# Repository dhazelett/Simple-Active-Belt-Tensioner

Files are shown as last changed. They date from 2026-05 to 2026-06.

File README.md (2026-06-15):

> 📢 **Important:** This is a _pre-release_ of the project and considered to be under active development and testing. If you're not prepared to do some tinkering and/or deal with initial usability issues, it is recommended that you do not attempt to build it right now and instead wait for the `v1.0` release

SABT Logo

Diagram

# Simple Active Belt Tensioner

A haptic device for sim racing, designed specifically for people who do not have a background in software or electronics.

It requires **no soldering or programming** and can be built for **as little as ~215 GBP** _including the harness_.

## What Is It?

Introduction Video (https://youtu.be/b3R1tQvu-o4)

An _active belt tensioner_ is a device that attaches between your sim rig and the anchor points of your racing harness. It dynamically tensions the harness in response to game telemetry; giving a sense of the forces you'd be experencing in a vehicle when changing speed, braking, cornering and jumping/landing.

It works with **any game fully supported by [SimHub](https://www.simhubdash.com/)**, but the current software is designed primarily for racing games and simulators.

This project consists of three parts:
- A shopping list of [components](#what-does-it-cost), readily available from online sellers
- Printable [parts](/Printables/) and instructions on how to assemble them
- A _SimHub_ plugin that controls the hardware and allows customisation of the effects

The printable files and software are **completely free** (except the required [SimHub License](https://www.simhubdash.com/get-a-license/)). The printed part designs are `CERN-OHL-P` licensed (open-source), and the software is `MIT` licensed, which essentially means you can do what you like with either; including selling printed/machined parts kits.

### Design Goals
- Lowest Practical Cost
- Minimal Parts & Tools
- No Soldering
- No Programming
- No 'Reclaimed' Parts
- Direct-Drive (FOC/BLDC) Performance & Flexibility

## Who Is It For?

Anyone with a sim rig that desires a more immersive experience. It's a plug-and-play design that requires no soldering or programming, so virtually anyone can build it.

Note that you'll need either an _aluminium profile_ (e.g. [GT Omega Prime](https://www.gtomega.co.uk/products/prime-cockpit)) or _2" tubular steel_ (e.g. [GT Omega Titan](https://www.gtomega.co.uk/products/titan-cockpit)) sim rig frame to mount this using the available brackets. Mounting to other types of rig is possible, but you'll need to design and fabricate your own brackets (or [get in touch](mailto:sabt@georgewilkins.co.uk) with me). _Folding-seat_ rigs (e.g. [Playseat Challenge](https://www.playseat.com/)) are _not suitable_.

I would recommend installing tactile transducers (bass shakers) before embarking on belt tensioners and other more exotic haptic systems. Transducers are by far the simplest and cheapest way of adding real immersion to your experience. They provide detail that belt tensioners cannot (road bumps, curbs, etc), while tensioners provide constant forces that transducers cannot (braking, cornering, etc).

### Community Builds
Several members of the sim racing community have [provided photographs](https://photos.app.goo.gl/ju7rso1PFKGxnRhJ8) of their SABT builds. Many have also _forked_ the project and customised it to their needs.

If you build a SABT, you're encouraged to photograph and document your completed installation. A good way to do that is by [creating a new](https://github.com/GeorgeWilkins/Simple-Active-Belt-Tensioner/discussions/new?category=sabt-builds) GitHub discussion.

## What Does It Cost?

If you have your own 3D printer, as little as **215 GBP** including taxes and delivery. If not, **250~300 GBP** depending on your choice of printed parts supplier.

### Purchased Parts
| Price (GBP) | Part | Notes |
| - | - | - |
| 120 | 2 x Motors | Provides the tensioning force |
| 20 | Controller | Provides USB control of the motors |
| 6 | 2 x Bearings | Allows the pulley covers to rotate smoothly |
| 7 | Screw & Nut Set | Provides every needed fastener in one set (with _many_ spares) |
| 5 | 1M Cord | A low-friction cord that winds around the pulleys (attached at the other end to your belts) |
| 20 | Power Supply | Provides DC power to the motors |
| 12 | Back Driving Protection Unit | Prevents power-supply resets if the motors are back-driven (**optional but recommended**) |
| 25 | 5-Point 2" Harness | A low-cost Aliexpress model or used/expired FIA harness |
| **215** | **Total** | ...excluding printables |

There is a [detailed parts list](/INSTRUCTIONS.md#motors-electronics--fixings) with sources in the build guide.

### Printing Options
| Price (GBP) | Method | Notes |
| - | - | - |
| 5~10 | Self-Print | Roughly 200g or 75M of filament |
| 30~60 | FDM Service | Assuming an _eBay-tier_ printing provider, not a professional company |
| 60~90 | MJF/SLS Service | [JLC3DP](http://jlc3dp.com/) and [3DPrintUK](http://3dprint-uk.co.uk/) used for reference pricing (nylon dyed black with peening) |

### Other Costs
Note that you will also need [SimHub Licensed Edition](https://www.simhubdash.com/get-a-license/) (currently **8 EUR** or more) to use this device. If you're reading this, you almost certainly already have it.

## How Does It Work?

The two motors are anchored to your rig with printed brackets. A self-orienting pulley is attached to the face of each motor.

The ends of each shoulder belt are attached to lengths UHMWPE/Dyneema cord, which are wrapped around each motor pulley.

When SimHub sends game telemetry to our plugin, it converts this into torque commands and send them to the motors over a serial connection.

## How Does It Perform?

Since we're using high-quality BLDC/FOC integrated servo motors, the effects are applied directly as _force_ (torque) rather than emulated by moving the belts a fixed distance, as with some DIY tensioners based on RC servos.

The benefits of this are:
- Smooth and silent operation
- Compact & clean design
- Auto-adjusting of the harness (adjustable idle tension)

The maximum force appliable by these motors with the current pulley design is about **10Kgf per belt**, putting us right around the rated mechanical loading for each motor. Imagine having **~10Kg of weights** attached to each belt hanging down from the back of your seat, and you'll get the idea.

This is plenty to give extra immersion and feedback, but significantly less than you'd feel in a real vehicle at motorsport velocities.

For comparison, the [QS-BT1](https://qubicsystem.com/product/qs-bt1) claims _"20.5kg per channel"_, but is a considerably larger and costs six times more.

Note that this system conveys progressive constant forces (cornering, braking, etc) rather than fine details (road texture, track kerbs, etc). For the latter, you should install one or more tactile transducers. The two work together to imply the sensation of movement without a costly motion simulator.

[Force Testing.webm](https://github.com/user-attachments/assets/be7b9d7a-be3f-46f7-abf1-9659297854bb)

## Anything I Should Be Aware Of?

There is considerable variation in rig, seat and harness designs, so I cannot anticipate every possible configuration. You'll need to decide if this system is suitable for your rig by looking at the installations examples and instructions.

Of particular note:
- The belt clamp designs are intended for 2" wide belts of up to 2MM thickness. If your belts are wider or thicker than this, you will need to modify the design (or let me know and I'll create additional designs)
- The need for belt rollers depends on the seat design. In many cases applying low-friction tape is sufficient. A 'universal' [Belt Roller](INSTRUCTIONS.md#belt-rollers) design is included should you wish to use it
- The system includes a design for a [Back Driving Protection Unit](INSTRUCTIONS.md#back-driving-protection), which prevents your power supply's protection circuitry from tripping when the motors are back-driven (e.g. by pulling fast on the belts). This is an optional component, but highly recommended. A _zero-soldering solution_ is available, but even the soldered version is very simple to assemble
- Although the motors and driver board can tolerate up to `24V` supply, I've found that `15V` is a good compromise. Operating at the maximum `24V` is not reccommended, because any voltage spikes risk damaging the motors. Common `19V` laptop power supplies have been tested and work; but the higher the voltage, the greater the risk of damage

## Is It Safe?

This is an open-source project involving powerful motors, pinch points and moving belts attached to your body.

⚠️ **No claims are made regarding the safety of this device. You are responsible for ensuring its safe use and no liability is accepted by the creator(s) for any damage or injury caused by this device.**

With that said, design measures have been taken with safety in mind. See [SAFETY.md](SAFETY.md) for details.

## How Do I Get Started?

Read through the [instructions](/INSTRUCTIONS.md) to get a better idea of what's involved and how to proceed.

> 📢 **Important:** This is a _pre-release_ of the project and considered to be under active development and testing. If you're not prepared to do some tinkering and/or deal with initial usability issues, it is recommended that you do not attempt to build it right now and instead wait for the `v1.0` release

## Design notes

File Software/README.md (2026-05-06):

# Software

There are two things you'll need to use this belt tensioner:
- [SimHub](https://www.simhubdash.com/) and a [License](https://www.simhubdash.com/get-a-license/) for 60FPS telemetry data
- The project's SimHub plugin, which must be copied into SimHub's installation directory

## Downloading SimHub

SimHub is going to already be on your machine or at least familiar to you if you have a sim rig. In case it's not, it's a popular utility in the Sim Racing community that collates and normalises telemtery data from various games and simulators, making it available to many devices and plugins. Our tensioner uses that telemetry to determine how much tension to apply to the belt at any given moment.

1. Go to [https://www.simhubdash.com/](https://www.simhubdash.com/) and click on `Download now` or the `Download` link at the top of the page
2. You'll see a large button, labelled something like `Download SimHub vX.X.X`, which will start the download when clicked
3. Unzip the downloaded file and run the executable within to install SimHub on your computer
4. Run SimHub at least once before attempting to install the plugin

## Licensing Simhub

The free version of SimHub offers 10Hz telemetry updates, which is sufficient for some devicces; but not for our tensioner. We'll need to buy a license to unlock 60Hz updates. It's cheap (as little as 8 EUR for a perpetual license) and absolutely worth the money.

Note that you do not need a _'Motion License'_ to use this tensioner; that is a more costly thing for full motion rigs. The regular license is sufficient for our needs.

1. Go to [https://www.simhubdash.com/](https://www.simhubdash.com/) and click on the `Get a license` link at the top of the page
2. Enter your details and complete payment
3. Grab the key from the e-mail you're sent and enter it into `Settings` > `General` > `Licenses` within SimHub
4. Once done you should see `Status: Licensed` at the bottom of the SimHub window

## Downloading & Installing The Plugin

1. Make sure _SimHub_ is closed before proceeding
2. Download the [SABT SimHub Plugin.zip](SABT%20SimHub%20Plugin.zip) file
3. Unzip the downloaded file, which will contain a `.dll` file (the plugin itself) and a `/Languages/` folder
3. Copy both into your SimHub installation directory (e.g. `C:\Program Files\SimHub`)
4. Open _SimHub_, which should then recognise the plugin and load it
5. Click on the `Simple Active Belt Tensioner` plugin in the left-hand menu and configure it as you like

You can change the language of the plugin (and SimHub itself) from `Settings` > `General` > `Language`.

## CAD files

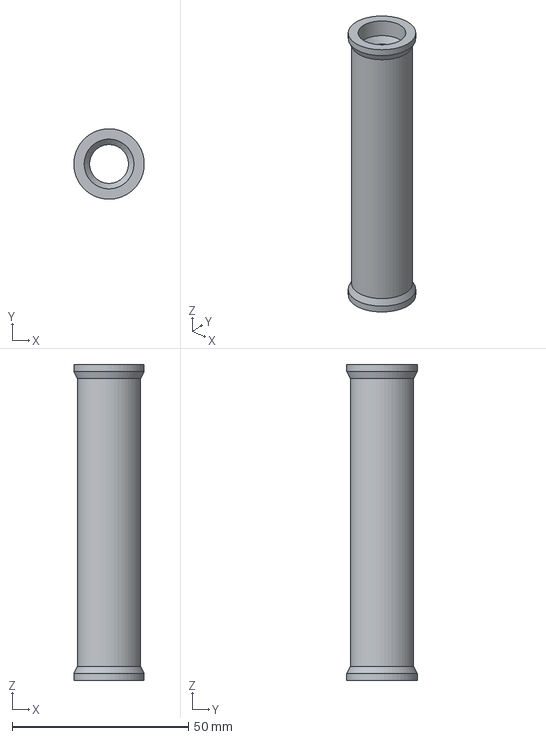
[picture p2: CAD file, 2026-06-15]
Printables/Belt Roller/Belt Roller (Roller).step
20.0 x 20.0 x 89.6 mm

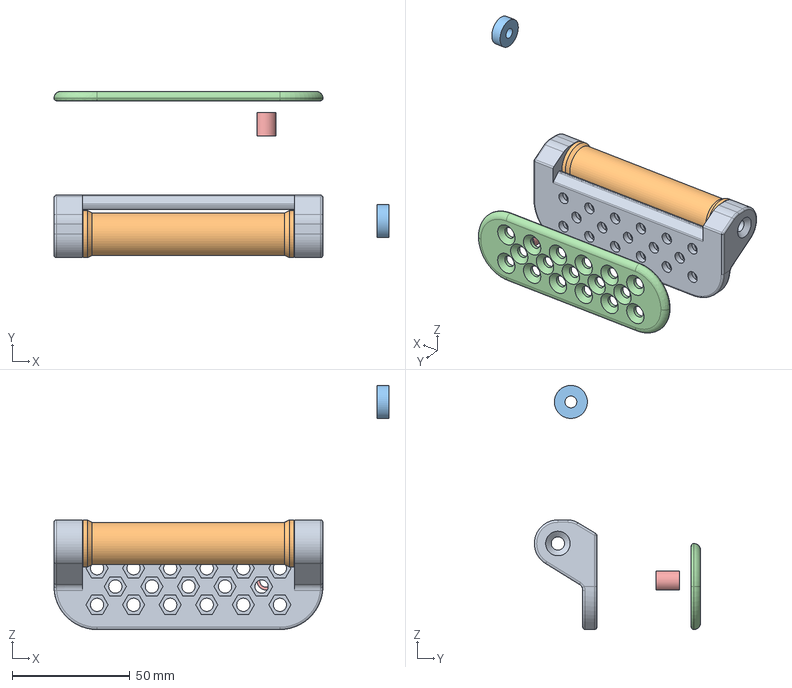
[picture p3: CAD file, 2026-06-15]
Sources/Printables/Belt Roller.FCStd
142.0 x 70.5 x 103.5 mm
Bracket
Roller
Bearing 5x14x5
Plate
Spacer

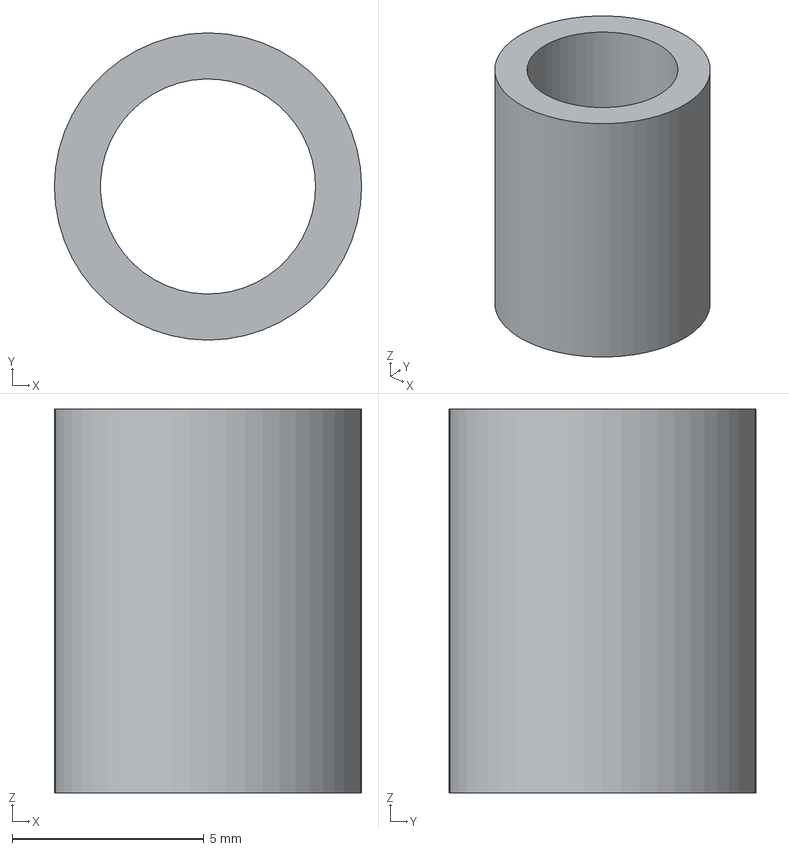
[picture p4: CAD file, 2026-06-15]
Printables/Belt Roller/Belt Roller (Spacer).step
8.00 x 8.00 x 10.0 mm

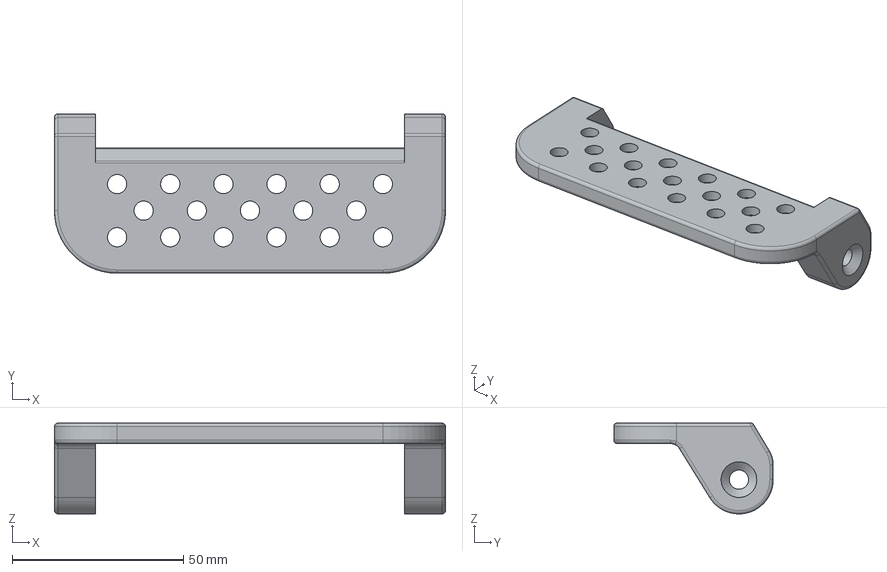
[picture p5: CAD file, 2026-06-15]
Printables/Belt Roller/Belt Roller (Bracket).step
114.0 x 46.5 x 26.5 mm

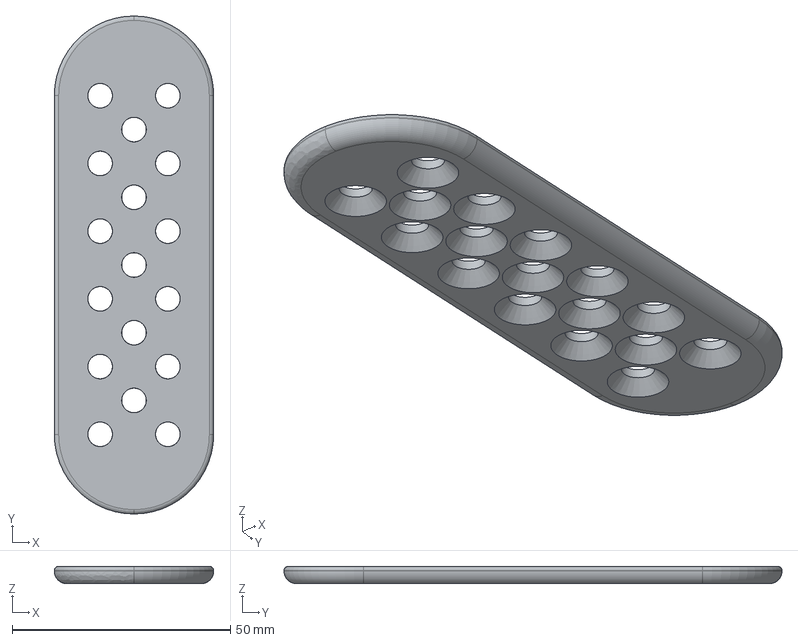
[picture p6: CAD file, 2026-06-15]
Printables/Belt Roller/Belt Roller (Plate).step
36.5 x 114.0 x 4.00 mm

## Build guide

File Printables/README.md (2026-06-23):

# Printables

The files in this directory and its sub-directories are what you need to print (or to have printed by a third party) to complete the kit.

Since there are a couple of options to choose from, you should read this before selecting and printing (or ordering) your parts.

### Choosing Your Brackets

Flat Motor Bracket (30~40mm Hole Spacing)

There are two main types of sim rig frame; _tubular_ and _profile_ (also known as _aluminium extrustion_):
- **Profile rigs** (e.g. [GT Omega Prime](https://www.gtomega.co.uk/products/prime-cockpit)) typically use `40-Series` aluminium extrusion that is bolted together in a modular fashion
- **Tubular frames** (e.g. [GT Omega Titan](https://www.gtomega.co.uk/products/titan-cockpit)) typically use `2"` steel tubing that is mandrel-bent into shape and welded together

If you have a _profile rig_, choose from the `Corner` or `Flat` profile bracket designs. In the latter case:
- The smaller `30~40mm Hole Spacing` version is suitable for most standard `30-series` and `40-series` profile
- The larger `50~90mm Hole Spacing` version is intended for larger or more unusual profiles

There are optional `Extra Tall` variants that provide an additional `50mm` distance between the motor and the mounting surface, for situations where you need to clear obstructions. These obviously use more material and will flex more under load. Use the standard height versions if you can.

If you have a _tubular frame_, choose the `Tube` clamp bracket design (which integrates with a commercial [truss clamp](https://www.amazon.co.uk/dp/B07DP1FK33) to attach to the tube).

You only need to print _two_ of a single type of bracket. The designs are all symetrical.

### Choosing Your Belt Clamps

Since there are a variety of belt types and terminations, a few options are available:
- **End Clamp**: This is designed to clamp the plain end of an unterminated 2" belt (suitable for bare belt ends, or belts you are happy to shorten to the ideal length)
- **Loop Clamp**: This is designed to loop through a 2" belt (up to 4mm thick) and secure back on itself using a standard belt buckle (likely to have come with your hanress)
- **Through Clamp**: This is designed to clamp anywhere along a 2" belt without needing to shorten or terminate the belt itself

The **Through Clamp** is probably the easiest to integrate, while the **End Clamp** is the neatest; but needing the belts to be shortened specifically for the tensioner (or shortened non-destructively with buckles).

### Opting For Belt Rollers

There's a lot of variation in seat design. In cases where the belt guides have horizontal bottom surfaces (perpendicular to your pulley cords), you don't _need_ belt rollers; the belts will just slide through the guides without issue. In this case low-friction tape _is_ recommended for a smoother experience and to protect your belt guides.

However with irregular or angled belt guides, you may run into issues with the belts bunching up in the corners of the guides and not sliding smoothly. For such cases, you can print and assemble two 'universal' [belt rollers](/Printables/Belt%20Roller/), which have been designed with an array of mounting holes to accommodate most belt guide shapes and angles.

These will not work well with curved belt guides (where they match the curvature of the seat). In such cases you may need to design your own version of the roller. You can use the [FreeCAD source file](/Sources/Printables/Belt%20Roller.FCStd) as a reference and starting point if so.

## Printables List

Regardless of your choices above, you should end up with:
- 2x Belt `End`|`Loop`|`Through` Clamp (Front)
- 2x Belt `End`|`Loop`|`Through` Clamp (Rear)
- 1x Controller Case (Top)
- 1x Controller Case (Base)
- 2x `Corner`|`Flat`|`Tube` Motor Bracket
- 2x Bearing Pulley (Cover)
- 2x Bearing Pulley (Face)
- 2x Bearing Pulley (Hub)

If you're making the [Back-Driving Protection Unit](/INSTRUCTIONS.md#back-driving-protection) you'll additionally need:
- 1x Back-Driving Protection Case (Top)
- 1x Back-Driving Protection Case (Base)

If you're making the [Belt Rollers](/Belt%20Rollers) you'll additionally need:
- 2x Belt Roller (Bracket)
- 2x Belt Roller (Plate)
- 2x Belt Roller (Roller)
- 4~8x Belt Roller (Spacer) \*

\* These are intended to be vertically scaled in your slicer software to be slightly shorter (by `~0.5mm`) than the depth of your belt guide (usually `12~40mm`). They help to prevent the bracket and plate from bending once clamped and also protect your belt guide plastics from the screw threads. It is recommended that you print the rollers and spacers together (in a vertical orientation) and the bracket and plate together (in a horizontal orientation).

### Self Printing

Obviously if you have your own 3D printer, you can print these yourself. These parts have been designed with hobby FDM printers in mind (not SLA/DLP/MSLA/LCD resin printers).

I've used [DEEPLE PLA Plus](https://www.amazon.co.uk/dp/B0F66H47J8) on my Bambu H2S for all of my own parts; but virtually _any_ strong PLA/ABS/PETG filament should be fine. Fibre-reinforced filament is okay for the mounting brackets but _not reccommended_ for the pulley parts.

As for printing settings, I would suggest:
| Setting | Value |
| - | - |
| Layer Height | `0.16` |
| Walls | `7` |
| Top Shell Layers | `7` |
| Bottom Shell Layers | `7` |
| Infill Density | `30%` |
| Supports | `Manual` |

Manually add supports to the counterbored bolt & nut holes _only_. They aren't needed anywhere else.

The above takes about **8 hours** on my H2S if printing everything at once. It uses about 75M of filament, or ~230g of PLA. I'd suggest you do the parts in smaller batchces though, to minimise wastage if something goes wrong during the print.

### Third-Party Printing

There are plenty of hobbyists on eBay offering low-cost FDM printing. Quality will depend very much on the individual seller.

If you want a more commercial-looking end result, there are companies running SLS/MJF machines which produce Nylon parts for reasonable money:
- [3DPrintUK](https://3dprint-uk.co.uk) are a provider of SLS/MJF Nylon parts in the UK. They have an instant quotation system that will give you a price right away (~**90 GBP** at the time of writing)
- [JLC3DP](https://jlc3dp.com) offer a similar service out of China with delivery to most countries

I've had test prints done in MJF Nylon PA12 (dyed black & shot peened) which came out great, but as with FDM printing, getting the tolerances correct for the press-fit bearings requires some trial and error.

FDM PLA (Left) &amp; MJF Nylon (Right)
FDM PLA (Left) &amp; MJF Nylon (Right)

### CNC Machining

At some point I'd love to see machined aluminium parts become available; but the parts included in this repository are very much designed for FDM printing, not CNC subtractive manufacturing.

Some of the parts would need to be adapted considerably to work with the latter process.

If you have the means to do this and want to make them available, please get in touch.

## Downloading

The printable files are provided in the `STEP` format. This provides the highest quality of geometry while being compatible with all major 3D printer slicing sofware _and_ commercial printing and CNC services.

GitHub treats these as _text_ files, so displays their contents rather than offering a download. To download a printable `STEP` file, use the `Download Raw File` option, which looks like a _tray and arrow_ icon:
Download STEP File

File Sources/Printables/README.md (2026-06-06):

# FreeCAD Source Files

If you're here looking for things to print, _you're in the wrong place_; go [here](/Printables) instead.

These files are the original [FreeCAD](https://www.freecad.org/) design files from which the printable `.STEP` files are generated. You'll only need these if you intend to change the designs of the parts.

| File | Part | Description |
| - | - | - |
| [Controller Case.FCStd](Controller%20Case.FCStd) | Electronics Case | The two halves of the **controller case** |
| [Back-Driving Protection Case.FCStd](Back-Driving%20Protection%20Case.FCStd) | Electronics Case | The two halves of the **back-driving protection unit case** |
| [Belt Roller.FCStd](Belt%20Roller.FCStd) | Belt Roller | The **belt roller** assembly |
| [Belt End Clamp.FCStd](Belt%20End%20Clamp.FCStd) | Belt Clamp | The two halves of a **belt clamp** (suitable for clamping the plain end of a 2" belt) |
| [Belt Loop Clamp.FCStd](Belt%20Loop%20Clamp.FCStd) | Belt Clamp | The two halves of a **belt clamp** (suitable for looping through a 2" belt) |
| [Belt Through Clamp.FCStd](Belt%20Through%20Clamp.FCStd) | Belt Clamp | The two halves of a **belt clamp** (suitable for clamping anywhere along a 2" belt) |
| [Corner Motor Bracket.FCStd](Corner%20Motor%20Bracket.FCStd) | Motor Bracket | A motor bracket designed to be **corner-mounted** to `30MM` or `40MM` aluminium profile |
| [Corner Motor Bracket (Extra Tall).FCStd](Corner%20Motor%20Bracket%20(Extra%20Tall).FCStd) | Motor Bracket | A motor bracket designed to be **corner-mounted** to `30MM` or `40MM` aluminium profile, with an additional `50mm` of motor distance from the mounting surface |
| [Flat Motor Bracket (30~40mm Hole Spacing).FCStd](Flat%20Motor%20Bracket%20(30~40mm%20Hole%20Spacing).FCStd) | Motor Bracket | A motor bracket designed to be **flat-mounted** to `30MM` or `40MM` aluminium profile |
| [Flat Motor Bracket (30~40mm Hole Spacing, Extra Tall).FCStd](Flat%20Motor%20Bracket%20(30~40mm%20Hole%20Spacing,%20Extra%20Tall).FCStd) | Motor Bracket | A motor bracket designed to be **flat-mounted** to `30MM` or `40MM` aluminium profile, with an additional `50mm` of motor distance from the mounting surface |
| [Flat Motor Bracket (50~90mm Hole Spacing).FCStd](Flat%20Motor%20Bracket%20(50~90mm%20Hole%20Spacing).FCStd) | Motor Bracket | A motor bracket designed to be **flat-mounted** to larger or more unusual aluminium profiles |
| [Flat Motor Bracket (50~90mm Hole Spacing, Extra Tall).FCStd](Flat%20Motor%20Bracket%20(50~90mm%20Hole%20Spacing,%20Extra%20Tall).FCStd) | Motor Bracket | A motor bracket designed to be **flat-mounted** to larger or more unusual aluminium profiles, with an additional `50mm` of motor distance from the mounting surface |
| [Tube Motor Bracket.FCStd](Tube%20Motor%20Bracket.FCStd) | Motor Bracket | A motor bracket designed to be **clamp-mounted** to `50MM` tube (requires [truss clamp](https://www.amazon.co.uk/dp/B07DP1FK33)) |
| [Pulley.FCStd](Pulley.FCStd) | Pulley Assembly | The **pulley** cover, hub and face parts |

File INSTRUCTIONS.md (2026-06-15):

# Instructions

Everything you need to know about building a tensioner of your own is in this document. Please make sure you at least skim through each section before proceeding.

## Printed Parts

See the [/Printables/](/Printables/) directory to obtain the printable files, and detailed information on printing them. Make sure you read through this document and note which printable parts you _actually need_.

## Ordering Components
### Motors, Electronics & Fixings

You should be able to order the _Waveshare_ [motors](https://www.waveshare.com/wiki/DDSM115) and [control board](http://www.waveshare.com/wiki/DDSM_Driver_HAT_(A)) from the same supplier, as they are almost always stocked together. They are designed for robotics projects, so those kinds of retailers are your best bet.

The rest of the parts can be obtained from virtually anywhere, including [Amazon](https://www.amazon.co.uk) or [AliExpress](https://www.aliexpress.com). Where I've linked to particular products, these are not endorsements or items I've tested; simply representative examples. Shop around, as prices change constantly...

| Guide Price | Part | Description | Example |
| - | - | - | - |
| `60 GBP` `x2` | 2 x `DDSM115` Motors | Waveshare BLDC FOC servo motors | [PiHut UK](https://thepihut.com/products/ddsm115-direct-drive-servo-motor) |
| `20 GBP` | `DDSM Driver HAT (A)` | Waveshare Controller Board (Version 'A' For `DDSM115` and `DDSM210`) | [PiHut UK](https://thepihut.com/products/ddsm-hub-motor-driver-board) |
| `6 GBP` | 2 x `6706` Bearings | `30x37x4mm` bearings for the pulleys | [Amazon UK](https://www.amazon.co.uk/dp/B0D4DN3RW8) |
| `7 GBP` | `M2.5` Screw & Nut Set | Eight `M2.5x16` (or `M2.5x18`) + eight `M2.5x10` + six `M2.5x12` + six `M2.5x20` + sixteen `M2.5` nuts | [Amazon UK](https://www.amazon.co.uk/dp/B0FSWHZPGD) |
| `5 GBP` | `~1M` UHMWPE/Dyneema Cord | The low-friction high-strength cord for the pulleys (`1.6~2.0MM` Diameter) | (any by-the-metre seller; eBay, etc) |
| `20 GBP` | `15V` `90W` DC Power Supply | The power supply for the board and motors (standard `5.5x2.5MM` centre-positive barrel plug) | [Amazon UK](https://www.amazon.co.uk/dp/B09RHC7QG9) |
| `25 GBP` | 5-Point `2"` Harness | A low-cost Aliexpress model or used/expired FIA harness | [AliExpress](https://www.aliexpress.com/item/1005008051519590.html) |

> 📢 **Important:**
> - The `DDSM115` motors are _sometimes_ sold in **pairs**. Make sure you're only buying _two motors_, not _two sets of two_
> - There are multiple motor models in the `DDSMXXX` series. Make sure you're buying the [DDSM115](https://www.waveshare.com/wiki/DDSM115)
> - There are multiple control board models of similar appearance. Make sure you're buying the [DDSM Driver HAT (A)](https://www.waveshare.com/wiki/DDSM_Driver_HAT_(A))
> - If using the _tubular_ brackets, you'll need to order two [2" Truss Clamps](https://www.amazon.co.uk/dp/B07DP1FK33), a pair of [`M10` Nuts](https://www.amazon.co.uk/dp/B0CGQVMP45) and [`M10x16MM` Low-Profile Bolts](https://www.amazon.co.uk/dp/B0DYHY2DHB)

### Belt Rollers

These are considered to be _optional_, but are usually required for seats with angled or irregularly shaped belt guides. They cost little to build, so are _recommended_ if you have any doubts about your seat's belt guide design or want maximum performance.

| Guide Price | Part | Description | Example |
| - | - | - | - |
| `5 GBP` | 4 x `605` Bearings | `5x14x5mm` bearings for the rollers | [Amazon UK](https://www.amazon.co.uk/dp/B0CZ8DJ6YM) / [Amazon UK](https://www.amazon.co.uk/dp/B0F6LNSC75) |
| `5 GBP` | 8 x `M5` Fully-Threaded Countersunk Bolts | Length depends on seat belt guide depth | [Amazon UK](https://www.amazon.co.uk/dp/B0C97LXKBP) |
| `5 GBP` | 8 x `M5` Hex Nuts (`8mm` WAF) | Must be `<5mm` thick | [Amazon UK](https://www.amazon.co.uk/dp/B0FMRFPWJ3) |

> 📢 **Important:**
> - Countersunk bolts are typically measured by their _entire length_ including the head
> - Measure your seat's belt guide/hole depth and _add_ `10mm`, rounding up to the nearest standard bolt length (e.g. my `39mm` belt guides need `50mm` bolts)
> - The bolts _must_ be fully threaded; otherwise you won't be able to use them for the roller axles
> - If you use bolts that are longer than needed, they may interfere with the belts and rollers

If _not_ using rollers, you can reduce friction (and wear) on your seat's belt loops if you apply some low-friction tape over the contact points. I've had success with [2-3/8" PTFE Tape](https://www.amazon.co.uk/dp/B0F3XKJW2V).

### Back-Driving Protection

You are _strongly encouraged_ to assemble and use this, as without it any rapid pulling on the belts may trigger the OVP/OCP within your power supply (as the motors act as _generators_ in this scenario) and disable tensioner functionality until time passes or a manual power supply reset is performed. There are a number of assembly and parts options detailed below. The [printable case](Printables/Back-Driving%20Protection%20Case) is designed to accommodate all of these options.

> ⚡ **Warning:** All of these options add a modest capacitance between the power supply and controller board. If you disconnect the protection unit, the capacitor may remain charged at up to `~15V` for a period of time. Do not touch or short the terminals at either end of the unit, as doing so **may cause a shock or damage equipment**.

The parts required will depend on your chosen option, but none should exceed `15 GBP` in cost:
- [Solderless + Ideal Diode](#solderless--ideal-diode): Using an ideal diode module with pre-soldered terminals
- [Soldered + Ideal Diode](#soldered--ideal-diode): Using an ideal diode module without terminals (requires soldering)
- [Discrete Schottky Diode](#discrete-schottky-diode): Using a discrete Schottky diode (requires _trickier_ soldering)

Back Driving Protection Options

#### Solderless + Ideal Diode

If you're at all uncomfortable with the idea of soldering or don't have the equipment, you can choose this option. You will need to cut and strip some wires, but no soldering is required.

We leverage the availability of premade 'Ideal Diode' modules with easy-to-use screw terminals and cheat a little by adding our capacitor across the output terminal, avoiding the need for any soldering at all.

| Guide Price | Part | Description | Example |
| - | - | - | - |
| `5 GBP` | Ideal Diode Module | A pre-made diode board with soldered screw terminals | [AliExpress](https://www.aliexpress.com/item/1005009419896467.html) |
| `5 GBP` | Capacitor | A `2200uF` `35V` electrolytic capacitor (just one; you'll have spares) | [Amazon UK](https://www.amazon.co.uk/dp/B07K87YFP9) |
| `5 GBP` | DC Cable | A `5.5x2.5mm` DC barrel plug to `XT60` adapter cable (or barrel-to-barrel extension)  | [Amazon UK](https://www.amazon.co.uk/dp/B0BPKNG672) or [Amazon UK](https://www.amazon.co.uk/dp/B0FJ8BKQCF) |

> 📢 **Important:** The printable case for the protection unit is intended for cables with a `5~5.5mm` external diameter, which is fairly typical. Any larger and you'll struggle to fit the cable into the ends of the case. Note also that the screw terminals on the diode board have a maximum gauge of roughly `10 AWG` (or `2.6mm` core diameter); though yours may vary.

The assembly instructions for this solderless option are included below under the [Assembly](#assembly) section.

#### Soldered + Ideal Diode

Soldered Option

This is essentially the same as the [Solderless + Ideal Diode](#solderless--ideal-diode) option; just using a premade 'Ideal Diode' module _without_ presoldered screw terimnals and soldering our wires and capacitor directly to the pads on the board.

As soldering jobs go this is very easy, and opens up many more options when it comes to 'Ideal Diode' modules. The one suggested for the solderless option can also be ordered without terminals and is a known good option; but you are not restricted to that specific module.

The main things you need to ensure of your chosen 'Ideal Diode' module are:
- The module actually blocks reverse current; not all such modules do (for 'OR-ing' purposes)
- The current handling exceeds `6A`
- The voltage handling exceeds `24V` (ideally `30V+`)
- The board has both `V+` and `GND` solder pads to make assembly easier (some omit the `GND` pads)

As long as these requirements are met, the module _should_ do the trick. These are some (unverified) examples:
- [Pololu 5382](https://www.pololu.com/product/5382)
- [Pololu 5383](https://www.pololu.com/product/5383)
- [Pololu 5388](https://www.pololu.com/product/5388)
- [Pololu 5389](https://www.pololu.com/product/5389)
- [Generic LM74700 Module](https://www.amazon.co.uk/dp/B0FNY9MWLX)
- [Generic 'Solar Diode' Module](https://www.amazon.co.uk/dp/B07QGW5J1H)

#### Discrete Schottky Diode

If you're a maker and familiar with electronics, a very simple circuit can be made using the same capacitor and any Schottky-like (e.g. SBR, SiC) diode with sufficient ratings. See above for the suggested values.

Strictly speaking this would be a downgrade from the 'Ideal Diode' style boards, but will still do the job just fine. Voltage drop is unlikely to be problematic with that class of diode, and the motors are wide-input.

See the diagrams above for a reference circuit design.

## Assembly

Depending on your choices above, some of these assembly instructions may not be relevant to you. Please read through the instructions and only follow the steps that are applicable to your build.

The photographs provided are for illustrative purposes and may not show the absolute latest part designs; don't worry if they aren't _exactly_ the same as the parts you've printed.

### Motors

| Step | Instructions | Illustration |
| :-: | :- | :-: |
| 1 | Since the motors are technically _wheels_, they come pre-fitted with rubber treads, which we need to remove.<br /><br />Unscrew the three `M2.5` bolts holding on motor face plate and remove it. You may need to remove a 'QA' sticker covering one of the screws.<br /><br />With the face plate removed, push the motor face (with the triangular hub) firmly with your thumbs, while holding the opposing face/rim of the tire with your fingers. Gradually working your way around the rim, moving small amounts at a time works best. | Wheel Motor |
| 2 | You'll be left with the bare motor. Keep the rubber tire, face plate and bolts safe though; in case you need to return the motors or repurpose them later. | Motor Without Tire |

### Pulleys

| Step | Instructions | Illustration |
| :-: | :- | :-: |
| 1 | Gather the four pulley parts; the bearing, the outer cover, the face plate and hub. | Pulley Parts |
| 2 | Press the bearing into the outer cover. This should be possible by hand. The accuracy/roughness of your print will dictate how easy this is.<br /><br />If the fit is too tight, use a hammer to _gently_ tap it in (alternating sides with each tap) or consider shaving away some material with a knife or file.<br /><br />If the fit is too loose, cut up a drinks can and shim around the edges of the bearing to fill in the gap (ensuring the shims do not protrude). | Inserting The BearingInserted Bearing |
| 3 | Insert the pulley face from the front so it sits inside the inner ring of the bearing. The notes above regarding fitting tolerances apply here too. | Face Inserted |
| 4 | Insert the pulley hub over the top, so that the triangular shape on the face part pushes into the triangular hole of the hub. They may pop together or be loose depending on the tolerances of your print (either is fine). The slot in the hub for the cord should be facing outward. | Hub Fitted |
| 6 | Cut a `0.5M` length of the _UHMWPE/Dyneema cord_ and tie a tight knot in the end, then remove any excess cord after the knot. | Knotting The Cord |
| 5 | Thread one end of the cord through one of the pulley cover holes. When assembling the _Left_ pulley, use the hole marked with `L` inside the pulley cover (or `R` for the _Right_ pulley). Push the knot into the cut-out in the pulley hub. It should stay in place relatively well. | Cord Inserted |
| 8 | Install the pulley onto the motor hub and insert and tighten three `M2.5x12MM` screws into the face plate. Make sure that the cord stays in the cut-out when doing so. | Installing The Pulley |

### Belt Clamps

| Step | Instructions | Illustration |
| :-: | --- | :-: |
| 1 | Gather the belt clamp parts; the four `M2.5x10` bolts, four `M2.5` nuts, and the front and rear plates. | Belt Clamp Parts |
| 1 | Insert `M2.5` nuts into the hexagonal holes on the underside of the rear clamp plate (as deeply as they will go). | Nuits Fitted |
| 2 | Tie a tight knot in other end of the cord you previously attached to the _Pulley_. Push the knot into the cut-out in the rear clamp plate, so the cord comes out the bottom. | Cord Fitted |
| 3 | Place the end of the harness belt into the rectangular detent of the rear clamp plate (it may overlap the knot; that's fine). Push the front clamp plate firmly down over both. | Belt PositionedClamp Applied |
| 4 | Keep pressure on the assembly while securing with the four `M2.5x10` bolts. Tighen each bolt partially in a circular pattern until they are all tight, rather than trying to fully tighten one at a time. | Tightening The Clamp |
| 5 | Once fully tightened, the two clamp parts should be fully touching with no visible gap between them. | Clamp TightenedClamp Fully Assembled |

### Brackets

| Step | Instructions | Illustration |
| :-: | --- | :-: |
| 1 | Gather the bracket parts; three `M2.5x20` bolts, the bracket and the motor (with or without pulley fitted). Since there are a number of bracket designs, the hardware needed to actually attach them to your rig will vary (but should be obvious if you already have a rig). | Bracket Parts |
| 1 | _Carefully_ feed the motor connectors and wires through the hole in the bracket. Bend back the smaller connector so you're not trying to push both through at once. | Folding Back The ConnectorWires Fed Through |
| 3 | Insert the motor stem into the socket on the braket. The shaft and socket are three-sided and symmetrical, so rotate it until it aligns with the socket and push in. As long as it sits fully into the socket, the angle doesn't matter. | Inserted The Motor |
| 2 | Secure the motor with the three `M2.5x20MM` bolts | Motor Bolted In |
| 3 | Attach the bracket to your rig frame. If using the _aluminium profile_ bracket designs, secure the bracket to your rig frame with suitable t-nuts and bolts. If using the tubular mount (with truss clamp), insert the `M10` nut into the printed backet slot, then secure it to the truss clamp with the `M10x16` bolt. | Assembled Bracket |

### Controller Board

| Step | Instructions | Illustration |
| :-: | --- | :-: |
| 1 | Gather the control board parts; the four `M2.5x16` bolts, four `M2.5` nuts, and the upper and lower shells. | Controller Board Parts |
| 2 | Flip the switch on the control board to the `USB` setting. | Switch Set To 'USB' |
| 3 | Insert `M2.5` nuts into the hexangonal holes on the underside of the lower printed case (as deeply as they will go). | Nuts Inserted |
| 4 | Insert the board into the lower half of the printed case. The _Raspberry Pi_ header on the rear may be a tight fit here; push down on the white circles either side of the header to press this in. | Board Inserted |
| 5 | Place the upper half of the case on top and secure with four `M2.5x16` bolts. | Case Assembled |

### Belt Rollers

| Step | Instructions | Illustration |
| :-: | --- | :-: |
| 1 | Gather the parts for each belt roller; the five `M5` bolts (length according to your belt guide depth), five `M5` nuts, three spacers, two `605` bearings, bracket, plate and roller. | Belt Roller Parts |
| 2 | Press-fit the bearings into the ends of the roller. | Fitting The Bearings |
| 3 | Insert two `M5` nuts into the inside faces of the bracket ends and thread in the `M5` bolts from the outside; no more than a couple turns (so their ends are flush with the nuts). | Inserting Nuts & Bolts |
| 4 | Position the roller between the bracket ends and start screwing in the bolts all the way, securing the roller in place. | Attaching The Roller |
| 5 | Take the partially assembled roller and remaining parts to your sim rig. | Partially Assembled |
| 6 | Establish where you'd like to mount the roller and which positioning holes you'll use. The roller must be as close to horizontal as possible and nideally cover the entire width of the belt guide hole. Horizontal guides only require two holes/bolts, while angled guides typically require three to prevent sideways movement. | Positioning |
| 7 | On the face plate, find the corresponding holes to the ones you previously chose and insert the `M5` bolts. Place the printed spacers over those. | Bolts & Spacers |
| 8 | Position the face plate inside the belt guide, with the bolts resting on the bottom face of the belt guide hole. At this point you may need to feed through your belt, as there may not be space to do so once the roller is fitted. | Face Plate |
| 9 | Line up the bracket with the face plate and bolts, then insert the `M5` nuts and tighten from the other side. The face plate and bracket should _lightly_ clamp to the front and back faces of the seat's belt guide. | Bracket Installation |
| 10 | Repeat for the other side and if you haven't already, feed the belts through and check that everything is moving freely. | Installed |

The choice of which holes to use is up to you and very much specific to your seat design. Below are some placement examples for common seat belt guide shapes. Note that horizontal belt guides can be fitted with only two `M5` positioning bolts, while angled guides usually need three to prevent sideways movement:

Belt Guide Shapes

### Back-Driving Protection

| Step | Instructions | Illustration |
| :-: | :- | :-: |
| 1 | Assemble the protection unit parts; the four `M2.5x16` bolts, four `M2.5` nuts, the capacitor, the diode board, the adapter cable and printed case. Cut the adapter cable in half as shown. | The Protection Unit Parts |
| 2 | Bend the capacitor legs as pictured, taking care not to damage the capacitor and noting the oritentation shown. If the legs of the screw terminals protrude significantly from the bottom of the board, take this opportunity to trim them down with some snips. | Preparing The Capacitor |
| 3 | Fully loosen the screw terminals. Insert the capacitor legs into the **output** screw terminals as shown (`GND` and `VOUT` on the board). with the capacitor `-` leg going into the board's `GND` as pictured. Do not tighten the terminals yet. | Fitting The Capacitor |
| 4 | Trim off roughly `6mm` of sheathing from the adapter cable ends and twist as shown. |  |
| 6 | Insert the bare wires into the screw terminals. The `XT60` cable should be on the **output** side and the round DC barrel cable should be on the **input** side. **Black** to `GND` and **red** to `VOUT` and `VIN`. Tighten up the screws as much as they will go. |  Inserting The Wires |
| 5 | Check for any stray or loose wires and adjust if needed. Install the unit into the printed case, taking care not to disturb the fitted wires. Make sure that the black outer sheath of the cable goes _completely inside_ the case as shown, so that the case lid can clamp down on it once closed. | Fitting Into The Case |
| 8 | Install the `M2.5x16MM` screws and nuts into the case and tighten as much as they will reasonably go. Ideally if you happen to have a multimeter, before attempting to power the controller board, check that the `XT60` connector produces the expected `15V` in the correct polarity (the **flat** side should be `+` and the **beveled** side `-`) when the power supply is connected to the dc barrel plug. |  The Completed Protection Unit |

## Wiring Up

Since the Waveshare board and motors are plug-and play, this is pretty straight forward.

If you're using the [Back-Driving Protection](#back-driving-protection), plug that into the control board (either the XT60 or DC Barrel sockets) and then into the power supply; otherwise just plug the power supply into the board directly.

If this is your first-time setup, your motors will need to be configured, so start with only a single motor plugged into the board. The plugin will tell you when to plug in the second motor.

It doesn't matter which of the exposed connectors on the top of the board you use for each motor. Make sure you've fully seated both the two-pin power plug and four-pin data plug.

Plug your USB type-c cable (one is supplied with the board) into the USB socket closest to the power connectors (marked `DDSM` on the board). If you use the other USB socket, it won't work.

If everything is connected correctly, the board will be detected by the SimHub plugin. No drivers are required.

> ⚠️ **Important:** Do not attempt to power or test the motors while not securely installed on the rig. If they start rotating while loose, they'll move around and potentially destroy themselves, the control board and the surface they are on

## Adjustment

Pulley & USB Port Guidance (https://www.youtube.com/watch?v=9At6qqblOZY)

If you already have a harness, you'll be accustomed to tightening it up with the buckles/straps it has. **You don't need to do that with this tensioner**, since it pre-tensions the harness for you (see `Idle Tension` in the `Tension` tab of the plugin).

However when first setting up the tensioner, you'll need to ensure the following:
- There is enough _plain belt_ (with no buckles or wider sections) to slide through the belt holes on your seat unhindered (allow for at least `20CM` of movement)
- Any excess belt is tucked/buckled away such that it does not catch or rub on anything

If you have excess shoulder belt length, you should run it through the seat holes and then buckle it back upon itself behind the seat (just above where you apply the tensioner's cord clamps).

Belt Clamps

The method of adjustment may depend on your chosen belt clamp design:
- **End Clamps**: These require the shortening of the harness shoulder belts, which is _strongly discouraged_ until you're 100% happy with your setup. Try using the belt buckles that likely came with your harness to make non-destructive adjustments to length first
- **Through Clamps**: Loosen the clamp bolts and simply slide the clamp up or down the length of the harness shoulder belts, then retighten in the desired location
- **Loop Clamps**: You'll already be using belt buckles to secure the looped harness shoulder belts against themselves, so simply adjust those buckles until you achieve the desired lengths

Adjustment

For reference, a _single turn_ of the pulley is about `~10CM` of cord. This is useful when working out how much cord you have wrapped around the enclosed pulley.

Since our harness is going to be self-adjusting (at least in the shoulders), we should make sure we have `~25CM` of cord between the belt clamps and the pulleys. Obviously we do not want our belt clamps colliding with the pulleys under normal operation.

We also want there to _always_ be at least some cord wrapped around the pulleys (`10~20CM`), as the motors will be unable to apply torque properly if the cord is fully unwound. Do not wrap more than `40CM` or about _four turns_ of cord, as this will start to bind the pulley.

Cord Wrapping

It is important that the cord is aligned such that it does not rub against the _sides_ of the pulley housing. The housing is designed to freely rotate with the cord at any angle along the axis of the motor; so if you move your chair backwards or forwards, it doesn't cause a problem. However the motor pulleys must line up perfectly underneath the seat's belt holes to avoid rubbing. In other words, the motor axles must be _perpendicular_ to the cords:

Pulley Alignment

_(Instructional Video TBC)_

## Software

See the [/Software/](/Software/) directory for the _SimHub_ plugin download and installation instructions.

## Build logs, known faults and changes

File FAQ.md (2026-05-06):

# Frequently Asked Questions

I try to address any common questions in the documentation itself; but that can clutter up or get lost amongst the most important information.

These are the most common questions raised:

- [Can I use a different type of motor?](#can-i-use-a-different-type-of-motor)
- [Can I use a different control board?](#can-i-use-a-different-control-board)
- [Why are there two USB ports on the control board?](#why-are-there-two-usb-ports-on-the-control-board)
- [Which power connector on the control board should I use?](#which-power-connector-on-the-control-board-should-i-use)
- [Why are the motors not being detected by the plugin?](#why-are-the-motors-not-being-detected-by-the-plugin)
- [I'm not getting much force from the belts](#im-not-getting-much-force-from-the-belts)

## Component Selection

> Can I use a different type of motor?

The BOM states the [Waveshare DDSM115](https://www.waveshare.com/wiki/DDSM115) motor should be used because that is the motor I've developed and tested with. However there appear to be a number of rebrands of the same OEM motor available around the world. For example, the [DFRobot M0601](https://wiki.dfrobot.com/fit1042/#tech_specs) is more commonly available in the US.

The company that makes these motors is [Direct Drive Tech](https://shop.directdrive.com/products/m0601c-111-direct-drive-motor), who appear to designate it the `M0601C-111`.

Since I have not purchased and tested these other versions I cannot recommend them until a user reports back that they work as expected. If that happens, I'll update the documentation.

As for other types of motors; no, both the printed pulleys and the Waveshare control board are designed to work specifically with the DDSM115 motor.

The SimHub plugin software is only programmed to use the DDSM115 motor protocol, so any other integrated servo motors you might find simply won't be controllable; even if you somehow manage to physically connect them.

Most comments/queries I've received regarding the motors have been from potential builders feeling they want more torque/force, which I don't personally feel is necessary. So far the people who have built the kit agree that the ~10Kg of force per belt is plenty.

If there is demand, a version of the kit for more powerful motors could be developed; but you'd likely lose the plug-and-play nature of the current design, requiring a custom PCB to control them.

> Can I use a different control board?

It would be possible to control the DDSM115 motors with a generic RS485-USB adapter board. In fact, that's one of the approaches I considered when designing the kit. However you'd need two of those adapters to run the motors separately (or add custom electonics to support both motors on a single adapter), and the SimHub plugin would need to be modified to support the different control hardware.

Generally it would be more expensive and complicated than just using the Waveshare control board.

If the project becomes popular there's a good chance I'll look at designing and manufacturing a custom board that integrates everything we need (including the back-driving protection circuitry), but for now the Waveshare board is a good off-the-shelf solution.

## Setup & Connectivity

> Why are there two USB ports on the control board?

The port we use is essentially a direct connection to the motor drivers via a USB to RS485 adapter that's built into the Waveshare control board. It allows a host PC to send commands directly to the motor drivers.

The other port connects to an ESP32 microcontroller on the control board, which also has access to the motor drivers and can be programmed to control the motors directly. That's what you'd use if working on a robotics project, which is what the control board is designed for.

In our case the SimHub plugin does the telemetry and force calculations needed for our belt tensioning, so we don't need to use the ESP32 at all. It would be possible to offload this processing to the ESP32; but that would require a firmware to be flashed to the ESP32 (making it more complex for non-technical users) and the calculations are so trivial for a PC to do that there is little reason to do so.

> Which power connector on the control board should I use?

There are two connectors on the board; a `5.5x2.5mm` DC barrel jack and an `XT60` socket. They are connected to each other, so it makes no electrical difference which one you use.

It is most likely that you have a power supply with a DC barrel plug, so that is what you'll use. The `XT60` connector is a better choice otherwise, as it is less likely to come loose when exposed to vibration and movement. However if you make sure to zip-tie (or otherwise secure) the power cable close to the control board, neither connection should be a problem.

## Troubleshooting

> Why are the motors not being detected by the plugin?

- Check that you've used the correct USB port on the control board (the one closest to the power inputs)
- Check that the control board is powered with 15V (and the correct polarity)
- If using the back-driving protection unit, check that it is functioning correctly. Try without it to see if it's causing a problem
- Check that the motor connectors are properly seated on the controller board

> I'm not getting much force from the belts

Have a look at the [setup instructions](INSTRUCTIONS.md) and check the following:
- Check that your cords are coming out of the pulleys at a perpendicular angle to the motor axles. They should not be touching the sides of the hole in the pulley (viewed from the side of the motor)
- When your harness is fitted and closed, there should be at least some cord wound around the pulleys. If not, the motors won't be able to apply torque to the belts as effectively as they could
- Check if your cord or belts are snagging on anything; consider adding low-friction tape to your seat's belt holes to reduce belt friction

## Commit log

2026-05-06 Adding note regarding other motor rebrands
2026-05-12 Updating printable sources list
2026-05-12 Updating bracket image
2026-05-25 Add action to toggle motors
2026-05-30 Adding auto-switching toggle & profile selection, tweaking language keys
2026-06-06 Adding belt roller design and partial documentation
    [Belt Roller (Bracket).step, Belt Roller (Plate).step, Belt Roller (Roller).step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]
2026-06-06 Adding belt guide diagrams and roller usage notes
2026-06-06 Adding belt roller assembly instructions & photos
2026-06-06 Refining BOM formatting and adding belt roller parts
2026-06-06 Updating diagram with more realistic belt guide holes
2026-06-06 Adding belt roller design link
2026-06-07 Amending guidance on positioning holes
2026-06-15 Updating belt roller source and printable designs
    [Belt Roller (Bracket).step, Belt Roller (Plate).step, Belt Roller (Roller).step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]
2026-06-15 Updating & reformatting documentation for easier reading
    [Belt Roller.FCStd]
2026-06-15 Cleaning up back-driving protection guidance and updating belt roller diagram
2026-06-19 fix(i18n): fix localisation strings in motor setup.
2026-06-23 Amending belt roller guidance
2026-06-27 Correcting state handling error during motor setup
